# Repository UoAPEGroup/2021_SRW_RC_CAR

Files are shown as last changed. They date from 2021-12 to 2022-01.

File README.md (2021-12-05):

# 2021_SRW_RC_CAR

Repo for work done during the summer workshop by the students on the RC car (2021-2022).

## Contributing

Create a branch for your feature / personal work and make changes in the relevant folders (i.e. Secondary/Hardware for members of the Pickup Hardware team).

When work is completed you make a "pull request" so others can review your work and then either changes will be requested or it will be "merged" into the main branch. This simplifies working in teams because everyone has their own "copy" (branch) and allows for greater flexibility.

For more information about branching see:

- git bash: [Atlassian tutorial](https://www.atlassian.com/git/tutorials/using-branches])
- Github Desktop: [the official tutorial](https://docs.github.com/en/desktop/contributing-and-collaborating-using-github-desktop/making-changes-in-a-branch/managing-branches)

## Teams 
1. Primary hardware/firmware
    - Kallum Spader
    - Suzanne Lo 
2. Magnetics
    - Ashley van der Merwe
    - Tor Larsen
3. Secondary (pick-up) hardware
    - Tim Cheng
    - Anthony White
    - Sree Bommineni 
4. Secondary (pick-up) firmware
    - Charley Shi
    - Martin Qiang 

## Software used
Our design was implemented with the aid of the following software: 
- Altium - for PCB design. 
- ANSYS Maxwell (via FlexIT) - for simulating magnetics. 
- MATLAB. 
- Plecs.
- Microchip (Atmel) Studio - for writing firmware. 
- Proteus - for simulating firmware. 

## Project overview 
[View PDF](Overview/project-overview.pdf)

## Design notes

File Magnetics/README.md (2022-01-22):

# Magnetics

This document outlines the final designs for the Primary and Pick-up Coils for the 2021 Summer Workshop RC Car design.

The design specifications are outlined below:

## Authors:
- Ashley
- Tor

## Description:
This "Magnetics" folder contains all of the magnetics simulations done for the primary and pickup coils to be used for the RC car design. The primary coils, which will go on track while the pickup coils would go onboard the RC car. 

## Specifications considered when designing the coils:
### Track Details:
- Length > 1000mm
- Width  = 300mm
- Tolerance ± 50mm
 
### Car details:
- Link: https://www.rchobbies.co.nz/tamiya-1-10-tt-02-subaru-impreza-monte-carlo-99-rc-car/
- Length: 16.6" (421mm)
- Width: 7.5" (190mm)
- Height: 3.8" (98mm)

### Primary Coil:
-  Coil:
    - Width = 300mm
    - Length = 1000mm
    - Height = 5mm
    
- Ferrite
    - Height = 8mm

### Secondary Coil:
- Coil
    - Width =  20mm
    - Length = 18mm
    - Height = 11mm

- Ferrite
  - Width = 109mm
  - Length = 15mm
  - Height = 8mm
  - Secondary coil is 15mm above primary coil

### Ferrite Placement:
2.5mm between the primary coil and ferrite layer

### Finding K:
- Keep k between 50% when car is moving.

## Final Design Values:
### Min Offset:
  - Lpt: 30.93uH
  - Lst: 7.345uH
  - k: 0.14
  - Isc: 2.49
  - Voc: 1.39
### Max Offset:
  - Lpt: 30.59uH
  - Lst: 7.37uH
  - k: 0.066
  - Isc: 1.44
  - Voc: 0.7

### Additional
Here is a link to a google doc with additional information about how the design was developed: https://docs.google.com/document/d/1CYPLc7FcOTWijb-OdK_4NrKyWV1d8R1uPq-4dlyw1d0/edit?usp=sharing

### Authors:
- Ashley v.d. Merwe
- Tor Larsen

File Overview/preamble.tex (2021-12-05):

\documentclass{article}
\usepackage[utf8]{inputenc}
\usepackage{tikz}
\usepackage{circuitikz}
\usepackage{hyperref}
\usepackage{float}
\usepackage{graphicx}

\usepackage{geometry}
\geometry{
a4paper,
top = 20mm,
bottom = 20mm,
left = 15mm,
right = 15mm,
}

\usepackage{parskip}
\setlength{\parindent}{0cm}

\title{IPT Summer Workshop Project Overview}
\author{2021 Summer Workshop Teams}
\date{December 2021}

\newcommand{\bd}{\textbf} % Bold 
\newcommand{\txt}{\textrm} % Text inside math mode. 
\newcommand{\subtxt}[1]{\textrm{\tiny{#1}}} % For subscript texts.

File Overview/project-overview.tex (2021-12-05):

\input{preamble.tex}

\begin{document}
    \maketitle

    \section{Introduction}
    In this project, the hardware and firmware required for the running of an RC car on a track using inductive power transfer (IPT) 
    technology. The RC car used is the \href{https://www.rchobbies.co.nz/tamiya-1-10-tt-02-subaru-impreza-monte-carlo-99-rc-car/}
    {TAMIYA 1/10 TT-02 SUBARU IMPREZA MONTE CARLO '99 RC CAR}. 

    \section{Track}
    The track will have a length $l$ and width $w$ as shown in Figure~\ref{track_top_view}. 
    \begin{figure}[H]
        \centering 
        \begin{tikzpicture}
            \draw[ultra thick](0,0) to ++(10,0) coordinate(A);
            \draw[dashed](A) to ++(0,3) coordinate(B);
            \draw[ultra thick](B) to ++(-10,0) coordinate(C);
            \draw[dashed](C) to ++(0,-3);  

            \draw[<->] (-0.5, 0) to ++(0,3); 
            \node at (-1,1.5) {$w$}; 

            \draw[<->] (0,-0.5) to ++(10,0); 
            \node at (5,-1) {$l$}; 

            \draw[blue, dashed] (3,2.45) rectangle (7.21,0.55); 
            \draw[dashed, red] (0,1.5) to ++(10,0); 

        \end{tikzpicture}
        \caption{Simplified sketch of track top view; blue dashed rectangle represents car.}\label{track_top_view}
    \end{figure}
    % Add a diagram showing what the tolerance means in our case. 

    For this project, the specifications are: 
    \begin{itemize}
        \item $l > 1000\rm mm$. 
        \item $w = 300\rm mm$. 
        \item Tolerance of car alignment\footnotemark: $\pm 50\rm mm$. 
    \end{itemize}
    \footnotetext{This is the maximum deviation of the center of the car from the center line 
        (red in Figure~\ref{track_top_view}) of the track.} % Verify this later. 

    \section{System diagrams}
    Our design can be partitioned into three main sections: 
    \begin{enumerate}
        \item The primary side. 
        \item The secondary (pick-up) side. 
        \item The motor driver. 
    \end{enumerate}

    \subsection{Primary side}
    \begin{figure}[H]
        \centering 
        \begin{circuitikz}[american]
            \node[fourport, scale = 2, t = (1)] (fullbridge) at (0,0){};
            \node[fourport, scale = 2, t = (2)] (compensation) at (5,0){}; 
            \node(fbtxt) at (0,-1) {Full bridge}; 
            \node(comptxt) at (5,-1) {Compensation}; 

            \draw(fullbridge.1) to[short] ++ (-2,0) node[ground] (gnd){};
            \draw(fullbridge.4) to[short] ++ (-2,0) to[V, l = $V_{\subtxt{IN}}$] (gnd);
            \draw(fullbridge.3) to[short] (compensation.4); 
            \draw(fullbridge.2) to[short] (compensation.1); 
            \draw(compensation.2) to[short] ++ (2,0) coordinate (A);
            \draw(compensation.3) to[short] ++ (2,0) to[L, l = $L_1$] (A);

        \end{circuitikz}
        \caption{System diagram for the primary side}\label{primary_sys_diagram}
    \end{figure}

    Figure~\ref{primary_sys_diagram} outlines the hardware of our primary side. 
    A DC voltage $30\txt{V}\leq V_{\subtxt{IN}}\leq 45\rm V$\footnote{Duleepa recommends 30V as the benchtop power supply in the labs can 
    be used to supply this voltage. The upper limit on $V_{\subtxt{IN}}$ ensures that it does not exceed about 48V above which 
    we cannot operate them in the labs.} % 
    is used as the input. As we must have AC for IPT to work\footnotemark, a \bd{full-bridge inverter} (1) transforms the DC voltage 
    to a high-frequency AC voltage. An \bd{LCL} compensation network (2) with partial series compensation follows it. 
    $L_1$ is the primary coil. 

    \footnotetext{As a changing current is required for a changing magnetic flux in the primary coil $L_1$, a DC 
    current will not cause any changing flux and hence voltage induced in the secondary. Only AC will suffice.}

    \subsection{Secondary side}
    Unlike the primary, the secondary employs \bd{parallel} compensation via the capacitor $C_{st}$. A rectifier followed 
    by a voltage regulator (3) % Check this with others later. Are we using a voltage regulator?  
    generates a DC voltage which is stepped up to $V_{\subtxt{OUT}}$ via a \bd{boost converter} (4). 
    $V_{\subtxt{OUT}}$ is optimally 10V\footnotemark~but can drop as low as 4V depending on the alignment of the car 
    with the center of the track. 

    \footnotetext{This is because the car's operating voltage is 10V. It can be operated down to 4V but it will 
    have inferior performance.}
    % Maybe add (hand-drawn) diagram about alignment here or in the section about the track later. 

    \begin{figure}[H]
        \centering 
        \begin{circuitikz}[american]
            \node[fourport, scale = 2, t = (3)] (reg) at (0,0){};
            \node[fourport, scale = 2, t = (4)] (boost) at (5,0){};
            \node(regtxt) at (0,-1) {Rectifier}; 
            \node(boosttxt) at (5,-1) {Boost converter}; 

            \draw(reg.1) to[short] ++ (-2,0) node[ground] (gnd){};
            \draw(reg.4) to[short] ++ (-2,0) coordinate (C) to[C, l = $C_{st}$, *-*] (gnd);
            \draw(C) to[short] ++ (-2,0) coordinate (D);
            \draw(gnd) to[short] ++ (-2,0) to[L, l = $L_2$] (D);

            \draw(reg.3) to[short] (boost.4); 
            \draw(reg.2) to[short] (boost.1); 
            \draw(boost.2) to[short] ++ (2,0) coordinate (A);
            \draw(boost.3) to[short] ++ (2,0) to[open, v = $V_{\subtxt{OUT}}$, o-o] (A);

        \end{circuitikz}
        \caption{System diagram for the secondary side}\label{secondary_sys_diagram}
    \end{figure}
    
    $L_2$ is the secondary coil. 

    \subsection{Motor driver}
    A pulse-width modulated (PWM) signal $v_{\subtxt{PWM}}$ used to drive the motor is produced via 
    a full-bridge inverter (5)\footnotemark. Depending 
    on its duty cycle, the average power delivered to the motor will vary accordingly. 

    \footnotetext{The microcontroller and hence firmware play a major role in this.}
    \begin{figure}[H]
        \centering 
        \begin{circuitikz}[american]
            \node[fourport, scale = 2, t = (5)] (fullbridge) at (0,0){};
            \node(fbtxt) at (0,-1) {Full bridge};

            \draw(fullbridge.4) to[short] ++ (-2,0) coordinate (A); 
            \draw(fullbridge.1) to[short] ++ (-2,0) coordinate (B);
            \draw(A) to[open, v = $V_{\subtxt{OUT}}$, o-o] (B); 
            
            \draw(fullbridge.3) to[short] ++ (2,0) coordinate (C);
            \draw(fullbridge.2) to[short] ++ (2,0) coordinate (D);
            \draw(C) to[open, v = $v_{\subtxt{PWM}}$, *-*] (D); 

            \draw(C) to[short] ++ (2,0) coordinate (E);
            \draw(D) to[short] ++ (2,0) coordinate (F);
            \draw(E) to[twoport, t = Motor] (F); 

        \end{circuitikz}
        \caption{System diagram for the motor driver}\label{motor_driver_sys_diagram}
    \end{figure} 

\end{document}

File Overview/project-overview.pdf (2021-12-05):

# IPT Summer Workshop Project Overview

2021 Summer Workshop Teams

December 2021

## 1 Introduction

In this project, the hardware and firmware required for the running of an RC car on a track using inductive power transfer (IPT) technology. The RC car used is the TAMIYA 1/10 TT-02 SUBARU IMPREZA MONTE CARLO ’99 RC CAR. (https://www.rchobbies.co.nz/tamiya-1-10-tt-02-subaru-impreza-monte-carlo-99-rc-car/)

## 2 Track

The track will have a length l and width w as shown in Figure 1.

w

l

Figure 1: Simplified sketch of track top view; blue dashed rectangle represents car.

For this project, the specifications are:
- l > 1000mm.
- w = 300mm.
- Tolerance of car alignment¹ : ±50mm.

## 3 System diagrams

Our design can be partitioned into three main sections:

1. The primary side.
2. The secondary (pick-up) side.
3. The motor driver.

1This is the maximum deviation of the center of the car from the center line (red in Figure 1) of the track.

1

### 3.1 Primary side

(1) (2)
Full bridge | Compensation

−

+ | VIN | L1

Figure 2: System diagram for the primary side

Figure 2 outlines the hardware of our primary side. A DC voltage 30V ≤ VIN ≤ 45V² is used as the input. As we must have AC for IPT to work³
, a full-bridge inverter (1) transforms the DC voltage to a high-frequency AC voltage. An LCL compensation network (2) with partial series compensation follows it. L1 is the primary coil.

### 3.2 Secondary side

Unlike the primary, the secondary employs parallel compensation via the capacitor Cst. A rectifier followed by a voltage regulator (3) generates a DC voltage which is stepped up to VOUT via a boost converter (4). VOUT is optimally 10V⁴ but can drop as low as 4V depending on the alignment of the car with the center of the track.

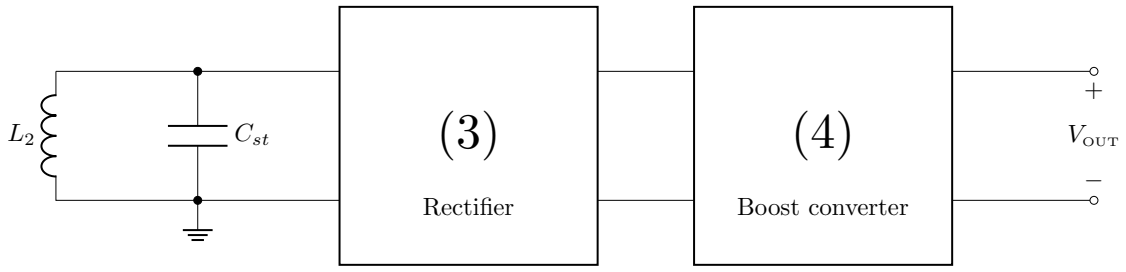
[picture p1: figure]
Rectifier; Boost converter; Cst; VOUT

Figure 3: System diagram for the secondary side

L2 is the secondary coil.

### 3.3 Motor driver

A pulse-width modulated (PWM) signal vPWM used to drive the motor is produced via a full-bridge inverter (5)⁵ .
Depending on its duty cycle, the average power delivered to the motor will vary accordingly.

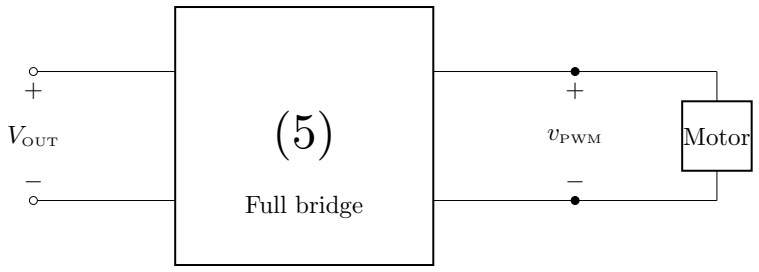
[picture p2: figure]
Full bridge; VOUT; vPWM; Motor

Figure 4: System diagram for the motor driver

2Duleepa recommends 30V as the benchtop power supply in the labs can be used to supply this voltage. The upper limit on VIN ensures that it does not exceed about 48V above which we cannot operate them in the labs.
3As a changing current is required for a changing magnetic flux in the primary coil L1, a DC current will not cause any changing flux and hence voltage induced in the secondary. Only AC will suffice.
4This is because the car’s operating voltage is 10V. It can be operated down to 4V but it will have inferior performance.
5The microcontroller and hence firmware play a major role in this.

2

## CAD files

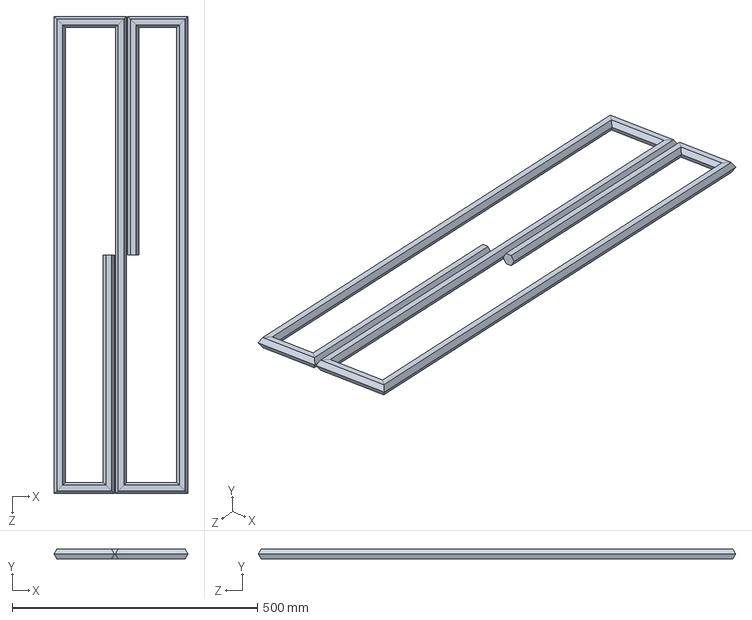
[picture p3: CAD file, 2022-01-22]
Magnetics/Tested coil designs/DoubleD/Double-D-modeled.STEP
273.1 x 20.0 x 973.1 mm

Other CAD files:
Magnetics/Final Coil Design/CadModels/Coil Designs.iam
Magnetics/Final Coil Design/CadModels/Coil Designs.ipn
Magnetics/Final Coil Design/CadModels/Drawing1.idw
Magnetics/Final Coil Design/CadModels/FerriteBar.ipt
Magnetics/Final Coil Design/CadModels/OldVersions/Coil Designs.0003.iam
Magnetics/Final Coil Design/CadModels/OldVersions/Coil Designs.0004.iam
Magnetics/Final Coil Design/CadModels/OldVersions/Coil Designs.0006.iam
Magnetics/Final Coil Design/CadModels/OldVersions/Part2.0001.ipt
Magnetics/Final Coil Design/CadModels/OldVersions/PrimaryCoilAluminiumLayer.0001.ipt
Magnetics/Final Coil Design/CadModels/OldVersions/PrimaryCoilAluminiumLayer.0002.ipt
Magnetics/Final Coil Design/CadModels/OldVersions/PrimaryCoilFerriteLayer.0001.ipt
Magnetics/Final Coil Design/CadModels/OldVersions/PrimaryCoilFerriteLayer.0002.ipt
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

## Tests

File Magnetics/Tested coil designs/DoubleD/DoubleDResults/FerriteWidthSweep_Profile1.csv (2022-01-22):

Variation | FerriteCoilGap | FerriteWidth | N | N2 | PrimaryCoilWidth | PrimaryCuttoutOffset | PrimaryCuttoutWidth | SCLength | SecondaryCoilThickness | SecondaryFerriteHeight | SecondaryFerriteLength | SecondaryFerriteWidth | SecondaryFerrriteOffset | secondaryYOffset | Start | Stop | Elapsed | Analysis Machine
1 | 10mm | 80mm | 10 | 10 | 5mm | 125mm | 75mm | 40mm | 5mm | 8mm | 100mm | 15mm | 30mm | 50mm | 11:38:03:323 | 11:46:03:298 | 00:07:59:975 | Local Machine
2 | 10mm | 100mm | 10 | 10 | 5mm | 125mm | 75mm | 40mm | 5mm | 8mm | 100mm | 15mm | 30mm | 50mm | 11:46:03:388 | 11:52:10:626 | 00:06:07:238 | Local Machine
3 | 10mm | 120mm | 10 | 10 | 5mm | 125mm | 75mm | 40mm | 5mm | 8mm | 100mm | 15mm | 30mm | 50mm | 11:52:10:718 | 11:58:09:418 | 00:05:58:700 | Local Machine
4 | 10mm | 140mm | 10 | 10 | 5mm | 125mm | 75mm | 40mm | 5mm | 8mm | 100mm | 15mm | 30mm | 50mm | 11:58:09:512 | 12:03:56:730 | 00:05:47:218 | Local Machine
5 | 10mm | 160mm | 10 | 10 | 5mm | 125mm | 75mm | 40mm | 5mm | 8mm | 100mm | 15mm | 30mm | 50mm | 12:03:56:831 | 12:10:28:856 | 00:06:32:025 | Local Machine
6 | 10mm | 180mm | 10 | 10 | 5mm | 125mm | 75mm | 40mm | 5mm | 8mm | 100mm | 15mm | 30mm | 50mm | 12:10:28:965 | 12:16:39:057 | 00:06:10:092 | Local Machine
7 | 10mm | 200mm | 10 | 10 | 5mm | 125mm | 75mm | 40mm | 5mm | 8mm | 100mm | 15mm | 30mm | 50mm | 12:16:39:171 | 12:20:56:693 | 00:04:17:522 | Local Machine
8 | 10mm | 220mm | 10 | 10 | 5mm | 125mm | 75mm | 40mm | 5mm | 8mm | 100mm | 15mm | 30mm | 50mm | 12:20:56:791 | 12:20:59:859 | 00:00:03:068 | Local Machine
9 | 10mm | 240mm | 10 | 10 | 5mm | 125mm | 75mm | 40mm | 5mm | 8mm | 100mm | 15mm | 30mm | 50mm | 12:20:59:978 | 12:25:05:464 | 00:04:05:486 | Local Machine
10 | 10mm | 260mm | 10 | 10 | 5mm | 125mm | 75mm | 40mm | 5mm | 8mm | 100mm | 15mm | 30mm | 50mm | 12:25:05:592 | 12:29:59:233 | 00:04:53:641 | Local Machine
11 | 10mm | 280mm | 10 | 10 | 5mm | 125mm | 75mm | 40mm | 5mm | 8mm | 100mm | 15mm | 30mm | 50mm | 12:29:59:370 | 12:35:02:628 | 00:05:03:258 | Local Machine
12 | 10mm | 300mm | 10 | 10 | 5mm | 125mm | 75mm | 40mm | 5mm | 8mm | 100mm | 15mm | 30mm | 50mm | 12:35:02:755 | 12:39:30:800 | 00:04:28:045 | Local Machine

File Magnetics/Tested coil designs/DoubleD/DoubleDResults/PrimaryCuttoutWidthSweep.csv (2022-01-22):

Variation | DiameterInner | FerriteCoilGap | FerriteWidth | N | N2 | PrimaryCuttoutOffset | PrimaryCuttoutWidth | SCLength | SCdepth | SCwidth | SecondaryFerriteHeight | SecondaryFerriteLength | SecondaryFerriteWidth | SecondaryFerrriteOffset | secondaryYOffset | Start | Stop | Elapsed | Analysis Machine
1 | 40mm | 10mm | 220mm | 20 | 20 | 125mm | 50mm | 40mm | 20mm | 20mm | 8mm | 100mm | 15mm | 25mm | 50mm | 17:11:28:246 | 17:15:04:352 | 00:03:36:106 | Local Machine
2 | 40mm | 10mm | 220mm | 20 | 20 | 125mm | 62.5mm | 40mm | 20mm | 20mm | 8mm | 100mm | 15mm | 25mm | 50mm | 17:15:04:403 | 17:18:34:970 | 00:03:30:567 | Local Machine
3 | 40mm | 10mm | 220mm | 20 | 20 | 125mm | 75mm | 40mm | 20mm | 20mm | 8mm | 100mm | 15mm | 25mm | 50mm | 17:18:35:030 | 17:21:58:609 | 00:03:23:579 | Local Machine
4 | 40mm | 10mm | 220mm | 20 | 20 | 125mm | 87.5mm | 40mm | 20mm | 20mm | 8mm | 100mm | 15mm | 25mm | 50mm | 17:21:58:665 | 17:25:46:246 | 00:03:47:581 | Local Machine
5 | 40mm | 10mm | 220mm | 20 | 20 | 125mm | 100mm | 40mm | 20mm | 20mm | 8mm | 100mm | 15mm | 25mm | 50mm | 17:25:46:313 | 17:29:13:513 | 00:03:27:200 | Local Machine
6 | 40mm | 10mm | 220mm | 20 | 20 | 125mm | 112.5mm | 40mm | 20mm | 20mm | 8mm | 100mm | 15mm | 25mm | 50mm | 17:29:13:582 | 17:33:12:112 | 00:03:58:530 | Local Machine
7 | 40mm | 10mm | 220mm | 20 | 20 | 125mm | 125mm | 40mm | 20mm | 20mm | 8mm | 100mm | 15mm | 25mm | 50mm | 17:33:12:172 | 17:37:34:880 | 00:04:22:708 | Local Machine

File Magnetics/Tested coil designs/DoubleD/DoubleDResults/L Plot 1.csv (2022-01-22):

PrimaryCoilWidth [mm] | Matrix1.L(Group1,Group1) [uH]
2.5 | 3.45515584354778
3 | 3.43269253857429
3.5 | 3.41150212866983
4 | 3.39671220020609
4.5 | 3.36830890029414
5 | 3.35106292450051
5.5 | 3.32906953925649
6 | 3.30868564845712
6.5 | 3.29081660415179
7 | 3.27276763116127
7.5 | 3.25228405255464
8 | 3.23606316680879
8.5 | 3.21765806227206
9 | 3.19720032211194
9.5 | 3.17686118751547
10 | 3.15761240952375
10.5 | 3.13914574697903

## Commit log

2021-12-10 Updated ReadMe for Magnetics section
2021-12-14 added Double D solidworks file
    [Double-D-modeled.SLDPRT, Double-D-modeled.STEP]
2021-12-15 Added LTSpice simulation with differential amplifier low pass filter, added params for pwm generation
2021-12-16 Altium schematic underway
    [Schematic.SchDoc, Workshop_Project.PrjPcb]
2021-12-17 Edited and cleaned up the draft LTSpice schematic.
2021-12-17 Schematic for first review
    [Schematic.SchDoc]
2021-12-17 Altium Schematic Draft (?)
    [Motor Controller.PrjPcb, MotorController.SchDoc]
2021-12-17 cleaned up schematic, parameterised title block
    [Schematic.SchDoc]
2021-12-17 added notes to altium schematic
    [Schematic.SchDoc]
2021-12-17 added notes from Duleepa
    [Schematic.SchDoc]
2021-12-21 First set of changes after schematic review
    [Schematic.SchDoc]
2021-12-28 changed regulators, created lug footprints
    [Schematic.SchDoc]
2021-12-30 updated schematic, turned into three pages
    [Bridge.SchDoc, Control.SchDoc, Converter.PcbDoc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]
2022-01-03 Mosfet timing to approximate current
2022-01-04 Corrected schematic nets and SMPS
    [Bridge.SchDoc, Control.SchDoc, Misc.SchDoc]
2022-01-07 modified I sense, Temperature sense and footprints
    [Bridge.SchDoc, Control.SchDoc, Converter.PcbDoc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]
2022-01-07 Added capacitor footprints and changed port types
    [Bridge.SchDoc, Control.SchDoc, Misc.SchDoc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]
2022-01-08 reannotated and updated pcb document
    [Bridge.SchDoc, Converter.PcbDoc, Misc.SchDoc]
2022-01-11 Schematic - reviewed notes, corrected driver; PCB - started power & converter
    [Bridge.SchDoc, Control.SchDoc, Converter.PcbDoc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]
2022-01-11 Updated the DoubleDCoil
    Updated DoubleDCoil and added some simulation results
    [FerriteWidthSweep_Profile1.csv, L Plot 1.csv, PrimaryCuttoutWidthSweep.csv]
2022-01-12 review push
    [Bridge.SchDoc, Control.SchDoc, Converter.PcbDoc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]
2022-01-12 Schematic changes made in accordance to review #2
    [Bridge.SchDoc, Control.SchDoc, Converter_V2.PcbDoc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]
2022-01-12 Removed PI controller feedback from output, moved to input.
    [MotorController.SchDoc]
2022-01-13 made ltos of changes
    [Bridge.SchDoc, DT.PcbDoc, Misc.SchDoc]
2022-01-13 did everything
    [Bridge.SchDoc, Control.SchDoc, DT.PcbDoc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]
2022-01-13 added zebra logo
    [DT.PcbDoc]
2022-01-13 finished first pass
    [DT.PcbDoc]
2022-01-14 v i A
    [DT.PcbDoc, Misc.SchDoc]
2022-01-14 Added switch
2022-01-14 VIA STITCHING
    [Control.SchDoc, DT.PcbDoc, Misc.SchDoc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]
2022-01-14 did everything x2
    [PCB.PcbDoc, Workshop_Project.PrjPcb]
2022-01-16 updated silkscreen with +/- indicators etc
    [PCB.PcbDoc]
2022-01-16 removed draft PCB documents
    [Workshop_Project.PrjPcb]
2022-01-17 Completed PCB
    [Misc.SchDoc, Workshop_Project.PrjPcb]
2022-01-17 renamed PCB doc
    [Workshop_Project.PrjPcb]
2022-01-18 Tidied PCB w/ Duleepa's improvements
2022-01-18 added cad models folder
    [Coil Designs.iam, FerriteBar.ipt, Part1.ipt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]
2022-01-19 Completed Bracket
    Finished the secondary bracket model
    [SecondaryBracket.0001.ipt, SecondaryBracket.ipt]
2022-01-21 Added Cad model and made final updates to the simulation
    [Coil Designs.0003.iam, Coil Designs.iam, Part2.0001.ipt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]
2022-01-21 Updated the CAD models
    [Coil Designs.0003.iam, Coil Designs.iam, FerriteBar.ipt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]
2022-01-22 Added Cad models to the final DD Coil Design
    [Coil Designs.0003.iam, Coil Designs.iam, FerriteBar.ipt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]
2022-01-25 Updated coil designs and corrected calculations with minor values
    [Coil Designs.0004.iam, Coil Designs.iam, Coil Designs.ipn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]
2022-01-26 Updated the CAD files and the Ansys files for the Primary coil
    [Coil Designs.0006.iam, Coil Designs.iam, PrimaryCoilFerriteLayer.0002.ipt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]
